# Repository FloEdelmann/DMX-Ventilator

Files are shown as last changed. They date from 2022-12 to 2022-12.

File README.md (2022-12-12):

# DMX-Ventilator

## Motivation

Wir waren im Dezember 2015 auf dem [Contact Indoor Festival München](https://www.facebook.com/events/544198745721461/ "Facebook-Versnataltung"). Was uns dort neben der Musik am meisten beeindruckt hat, waren die Ventilatoren, die als Effektgeräte hinter der Bühne im Zenith&nbsp;I heruntergelassen werden und sich drehen konnten. Die Flügel haben in einer einstellbaren Farbe geleuchtet und auch die Geschwindigkeit war in einem weiten Bereich regelbar.

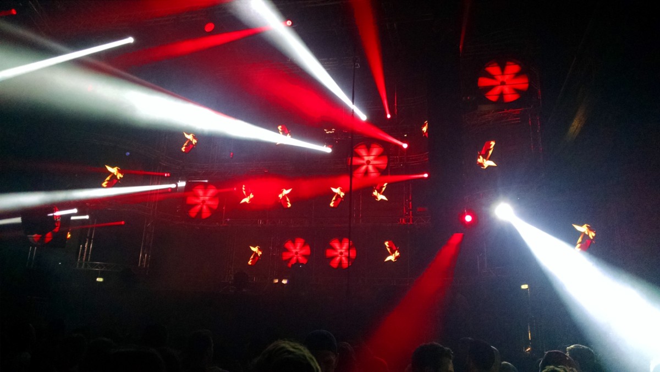
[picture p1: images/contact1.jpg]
Ventilatoren auf dem Contact-Festival 1

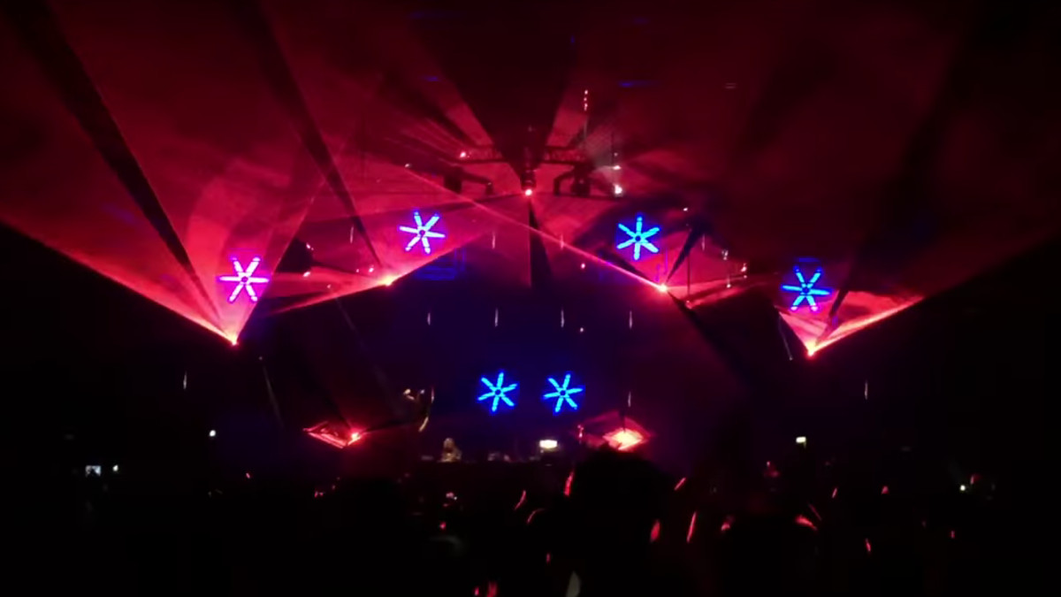
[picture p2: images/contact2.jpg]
Ventilatoren auf dem Contact-Festival 2


Auf YouTube gibt es sie auch in Bewegung zu sehen:
https://www.youtube.com/watch?v=OpufAzwtyVI (rot in verschiedenen Geschwindigkeiten)
https://www.youtube.com/watch?v=SzctCUNd09I (blau)

So etwas wollten wir jetzt auch auch!

## Planung

### Elektronik

Bei der Suche nach DMX-Selbstbau-Projekten verweist letztendlich fast jede Quelle auf [Hendrik Hölschers Seiten](http://www.hoelscher-hi.de/hendrik/wahl.htm). Sein [DMX-LED-Dimmer](http://www.hoelscher-hi.de/hendrik/light/dmxled.htm) hat schon einige Features, die auch unser Ventilator haben soll: Über DMX können 8 Kanäle gesteuert werden (zusätzlich sogar gestrobed), dank AVR-Microcontroller ist die Schaltung einfach zu programmieren und zu verändern und die Hardware ist sehr modular gehalten, sodass auch andere Projekte einfach realisiert werden können.

Es fehlt jedoch die Ansteuerung eines Motors. Außerdem wollen wir LED-Strips verwenden, da sie einfach zu montieren sind, und die brauchen noch eine extra Stromversorgung. Also muss eine zweite Platine her, die die Ansteuerungen übernimmt. Sie ist so gelayoutet, dass auch ein Lochraster-Aufbau möglich ist.

Beide Schaltungen hängen dann zusammen an einer 12V-<abbr title="Gleichspannung">DC</abbr>-Stromversorgung und werden über die 8-polige Steckerleiste miteinander verbunden.

Zum Programmieren des Microcontrollers werden über den ISP-Port die nötigen Anschlüsse herausgeführt. Da es jedoch ein standardisiertes 10-Pin-ISP-Interface gibt, das auch die gängigen [Programmieradapter](http://www.mikrocontroller.net/articles/AVR_In_System_Programmer) verwenden, habe ich mir ein zusätzliches Adapterkabel gebaut.

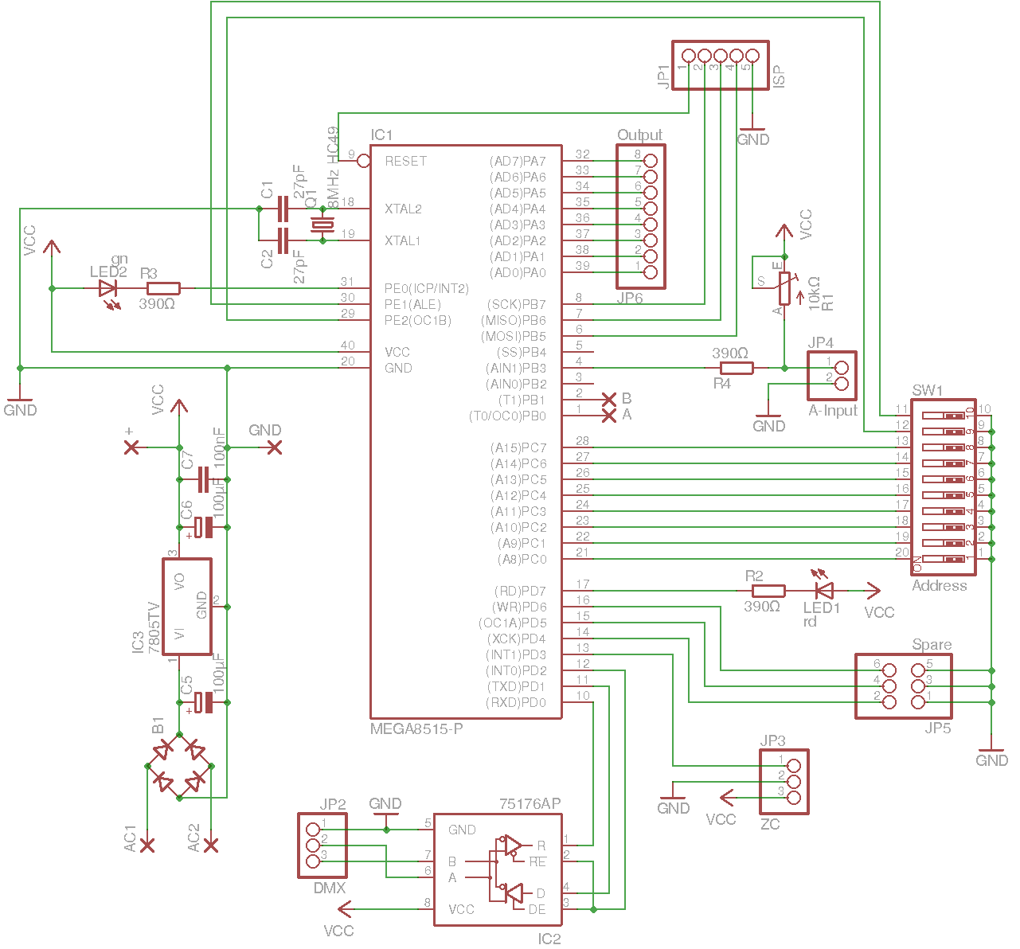
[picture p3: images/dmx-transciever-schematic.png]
Layout des DMX-Transcievers

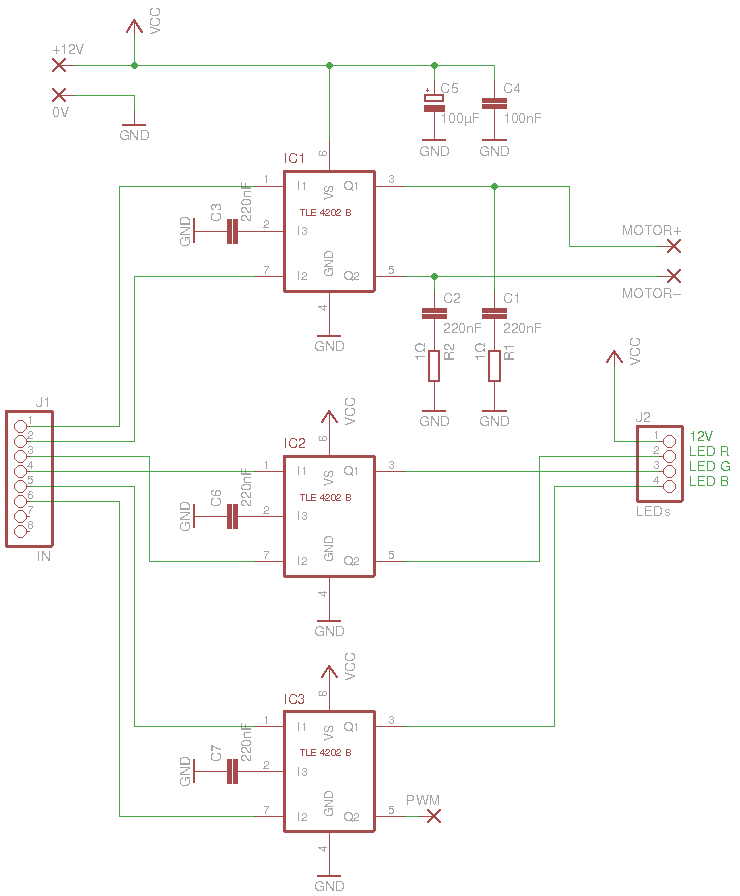
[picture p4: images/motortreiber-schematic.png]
Schaltplan des Motortreibers

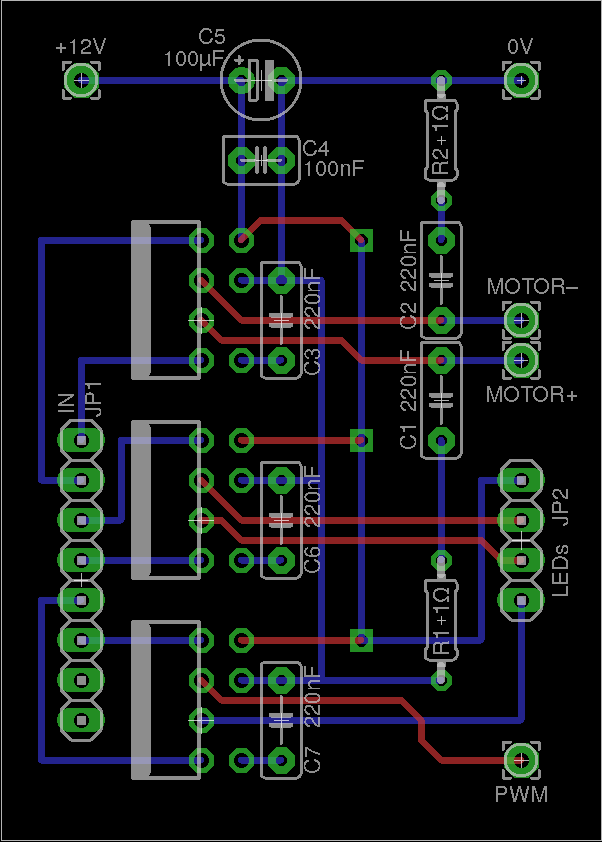
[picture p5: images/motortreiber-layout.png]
Layout des Motortreibers

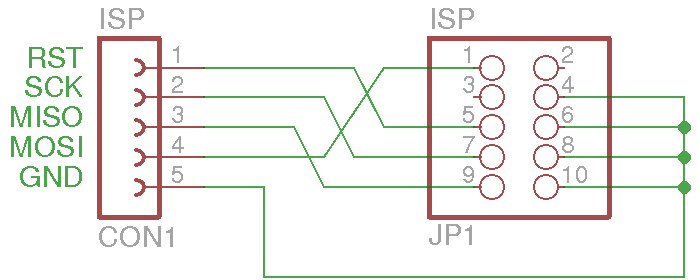
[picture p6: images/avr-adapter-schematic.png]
Anschlussplan des Adapterkabels

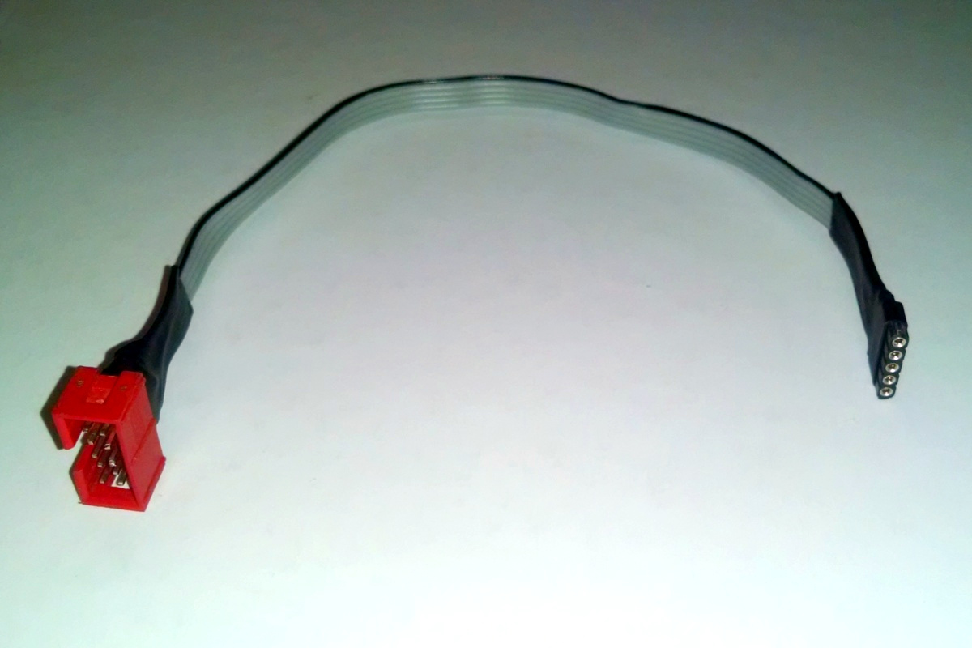
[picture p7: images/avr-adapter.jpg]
Adapterkabel

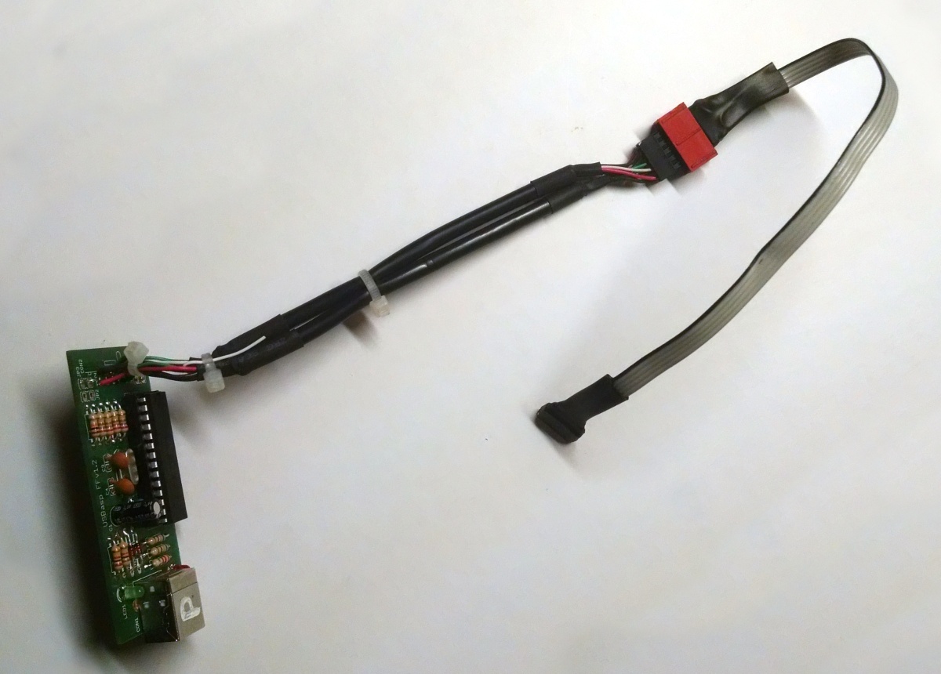
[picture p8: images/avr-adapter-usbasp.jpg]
Adapterkabel an der Programmierplatine USBasp


**Downloads für [EAGLE](http://www.cadsoft.de/download-eagle/):** [avr-adapter.sch](eagle/avr-adapter.sch), [dmx-transciever.sch](eagle/dmx-transciever.sch), [motortreiber.brd](eagle/motortreiber.brd), [motortreiber.sch](eagle/motortreiber.sch)

### Gehäuse & Mechanik

Am Motor wird eine Edelstahlwelle befestigt, die von einem Kugellager drehbar in Position gehalten wird. Die Rotorblätter sollen aus milchigem Plexiglas geschnitten werden, da diese als Lichtleiter bei der Anstrahlung mit den LED-Strips hoffentlich eine gute Ausleuchtung erzielen. Sie werden zwischen zwei großen Beilagscheiben mit mehreren Schrauben / Nieten befestigt und als ganzes von vorne an die Achse geschraubt.

Mit [Autodesk 123D Design](http://www.123dapp.com/design) lässt sich recht schnell ein vorzeigbares 3D-Modell erstellen. Dabei kann man schon vor dem physischen Aufbau Mängel in der Konstruktion erkennen und beheben.

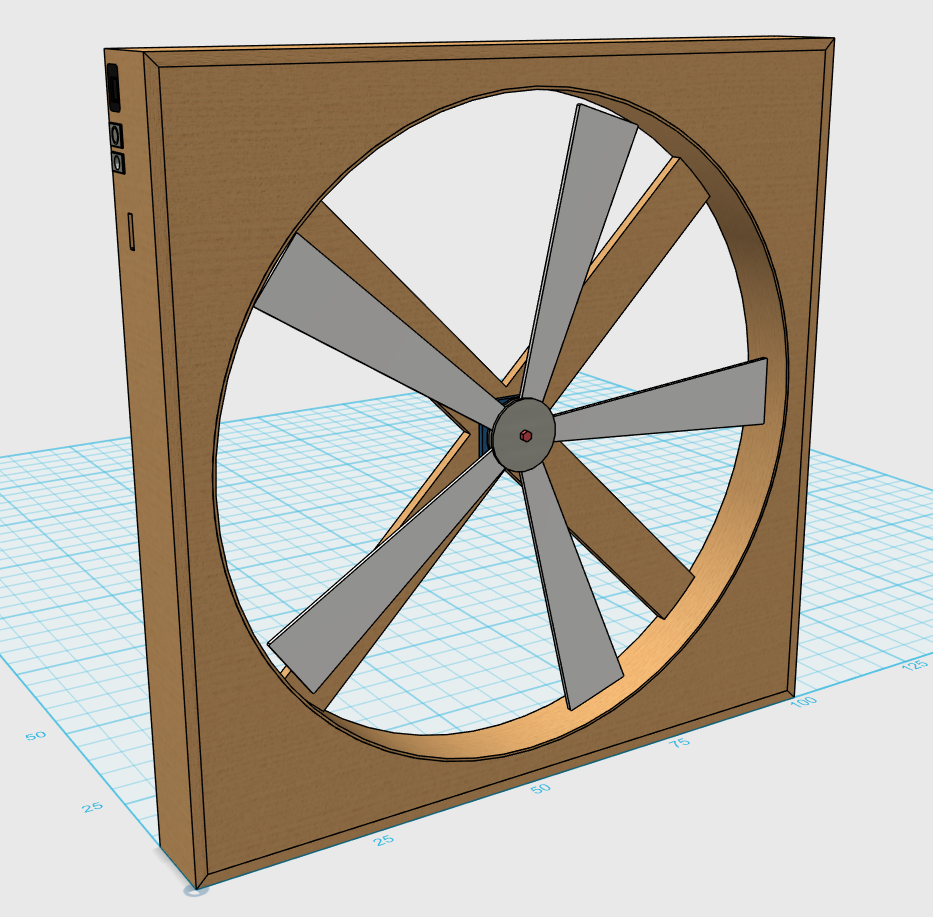
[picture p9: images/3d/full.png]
Gesamtansicht

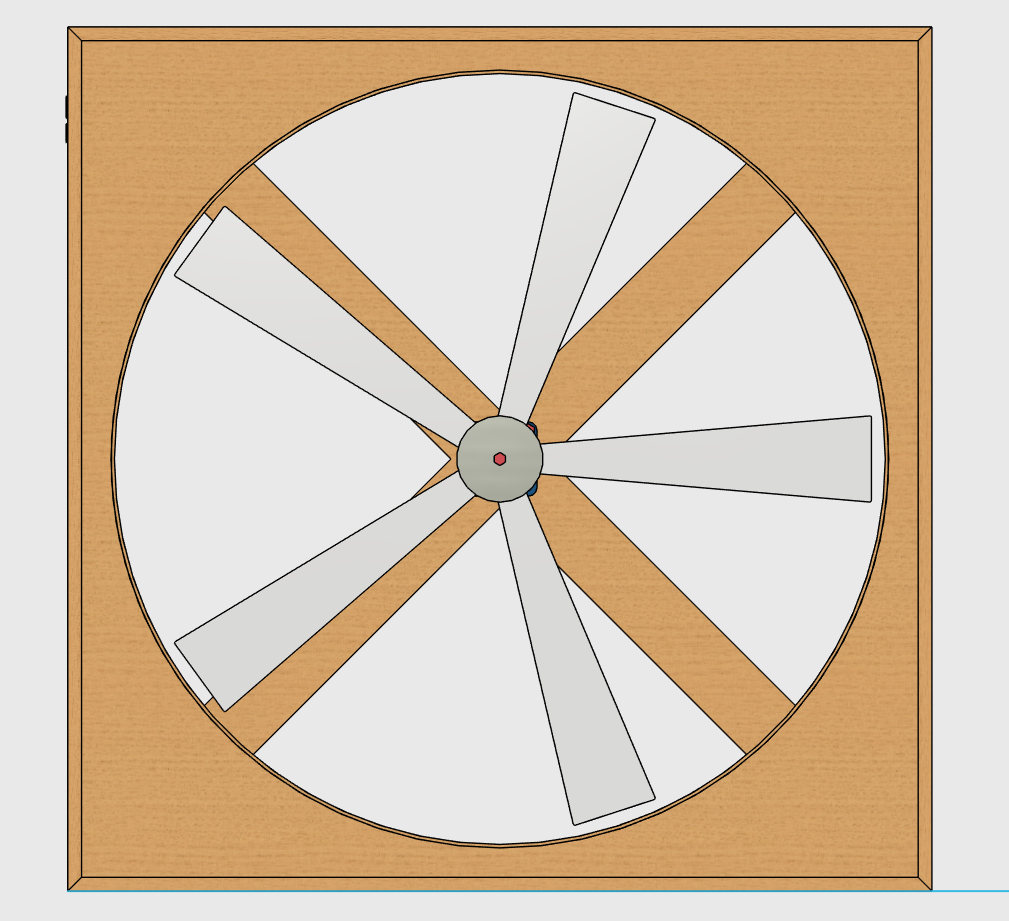
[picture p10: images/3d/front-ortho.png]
Frontansicht (orthografische Projektion)

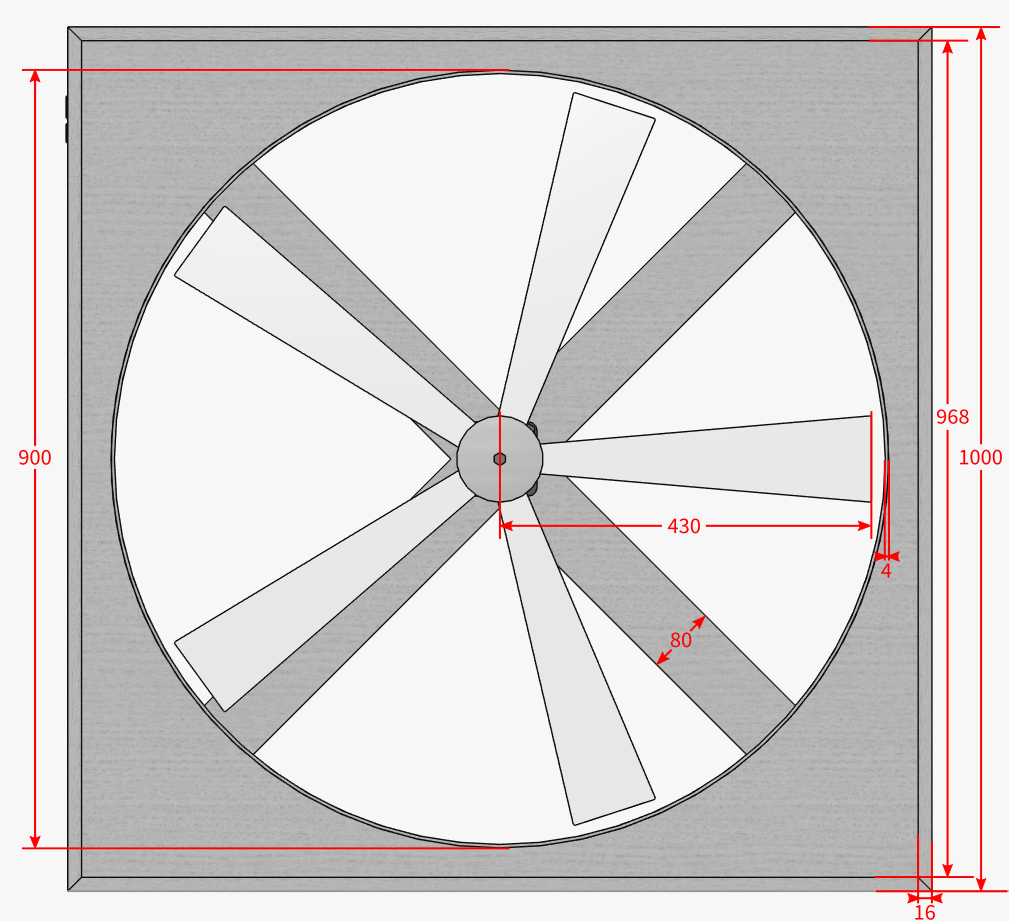
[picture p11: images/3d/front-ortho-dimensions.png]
Frontansicht mit Maßen

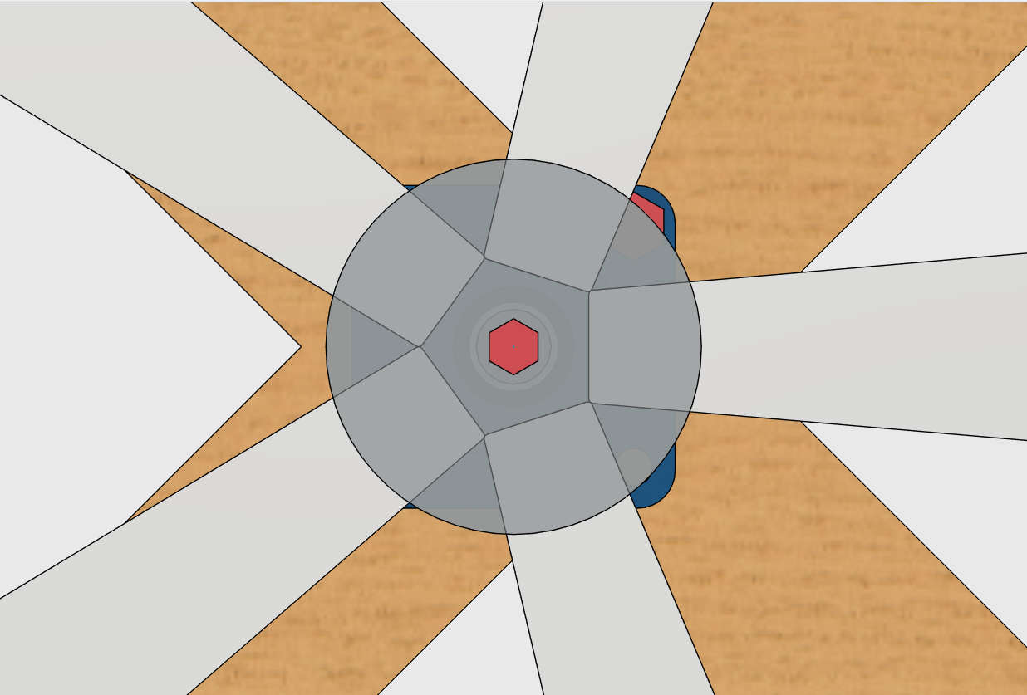
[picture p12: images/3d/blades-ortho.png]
Flügel (orthografisch)

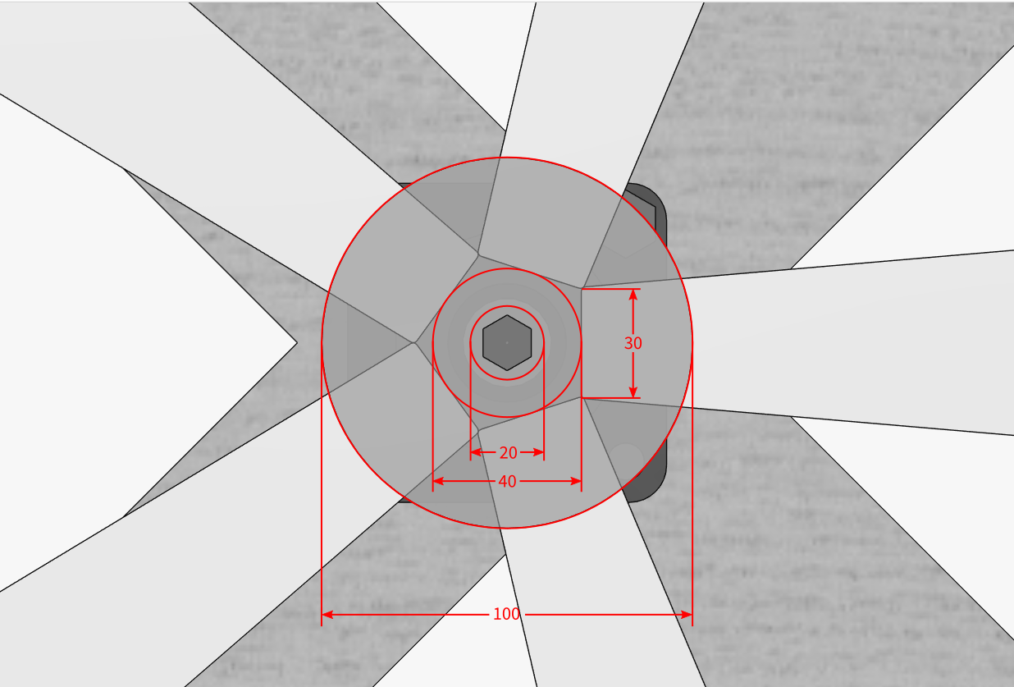
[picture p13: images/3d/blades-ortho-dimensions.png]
Flügel mit Maßen

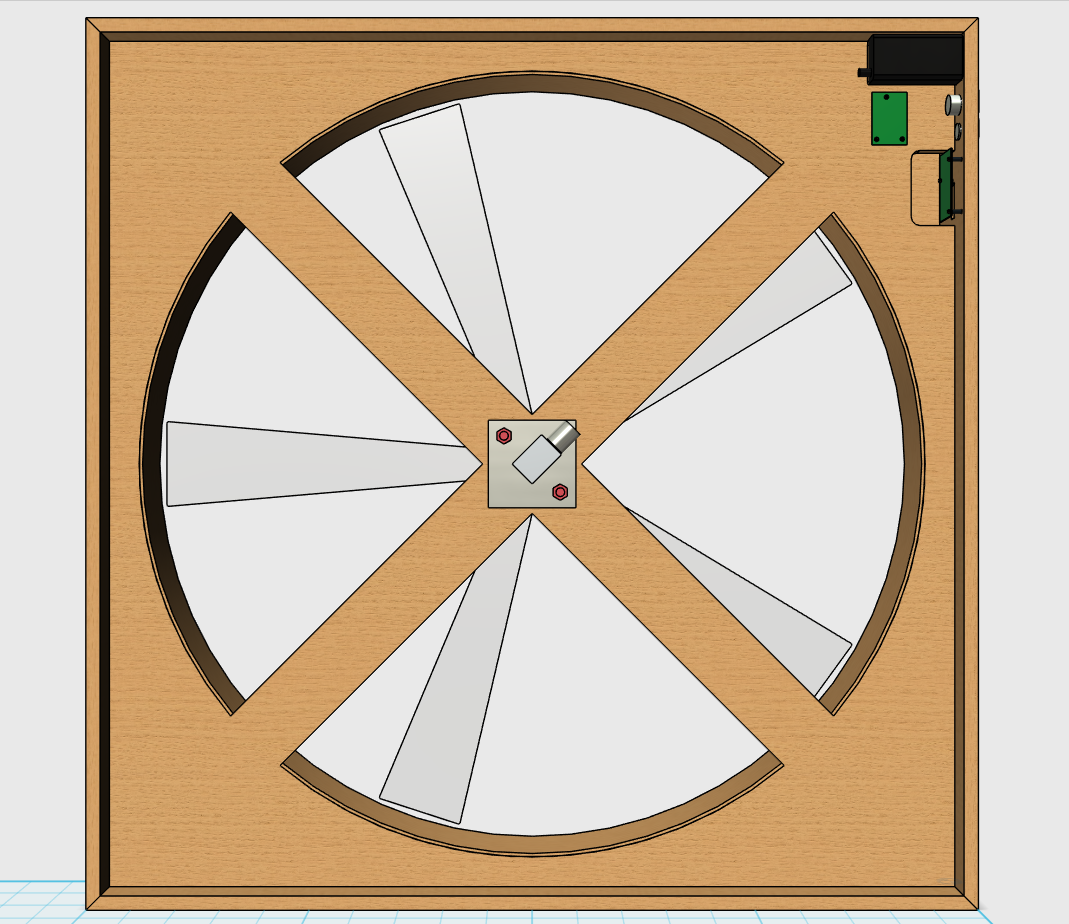
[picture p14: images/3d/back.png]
Rückansicht

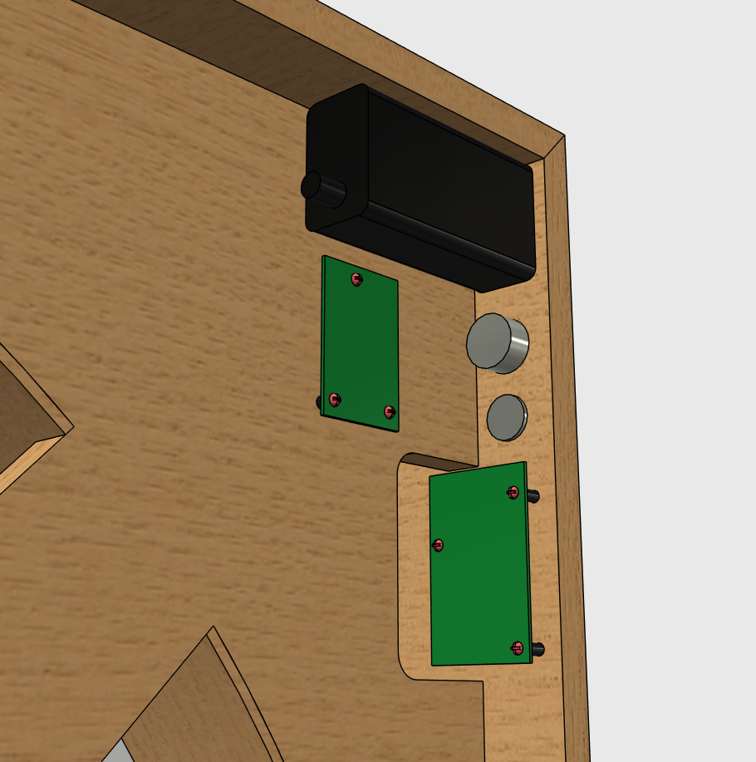
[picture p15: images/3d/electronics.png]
Elektronik

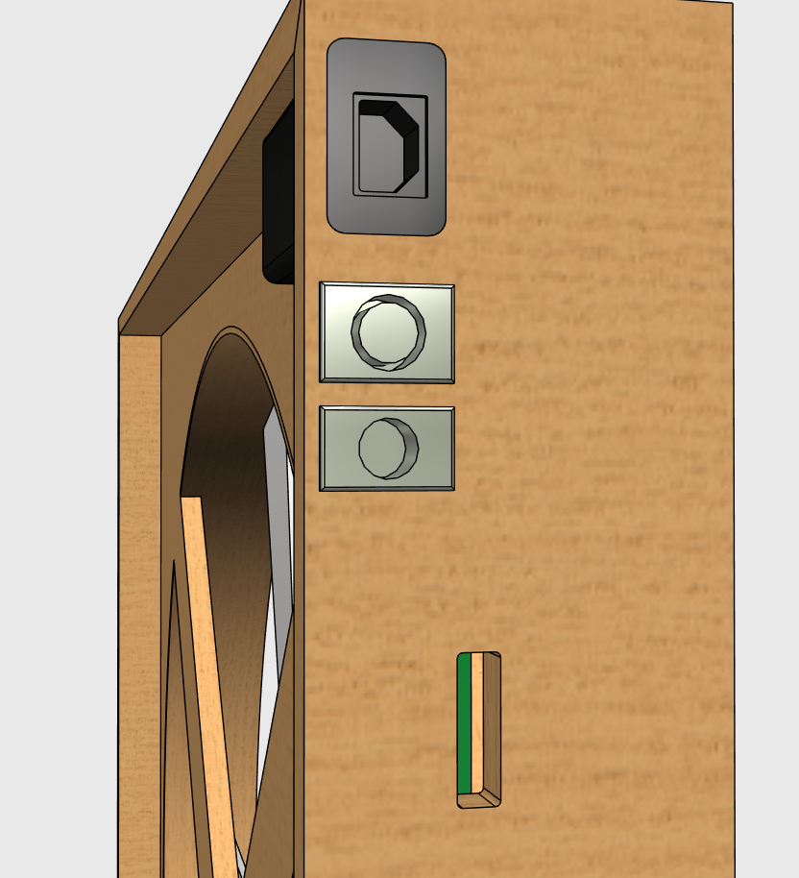
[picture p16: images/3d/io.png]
Anschlüsse mit Aussparung für DIP-Switch und Status-LEDs

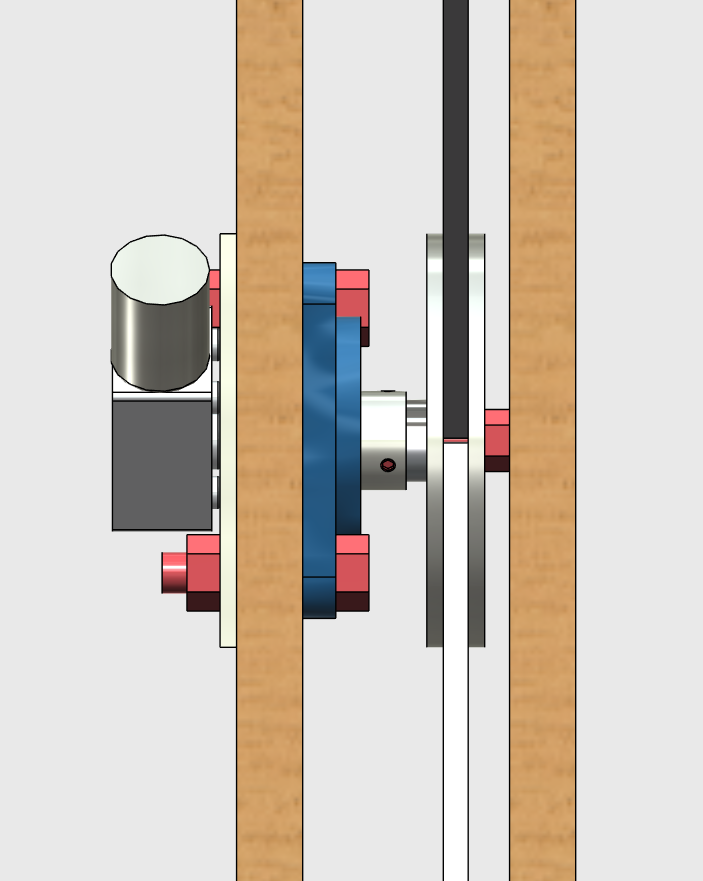
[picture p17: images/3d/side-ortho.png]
Seite (orthografisch)

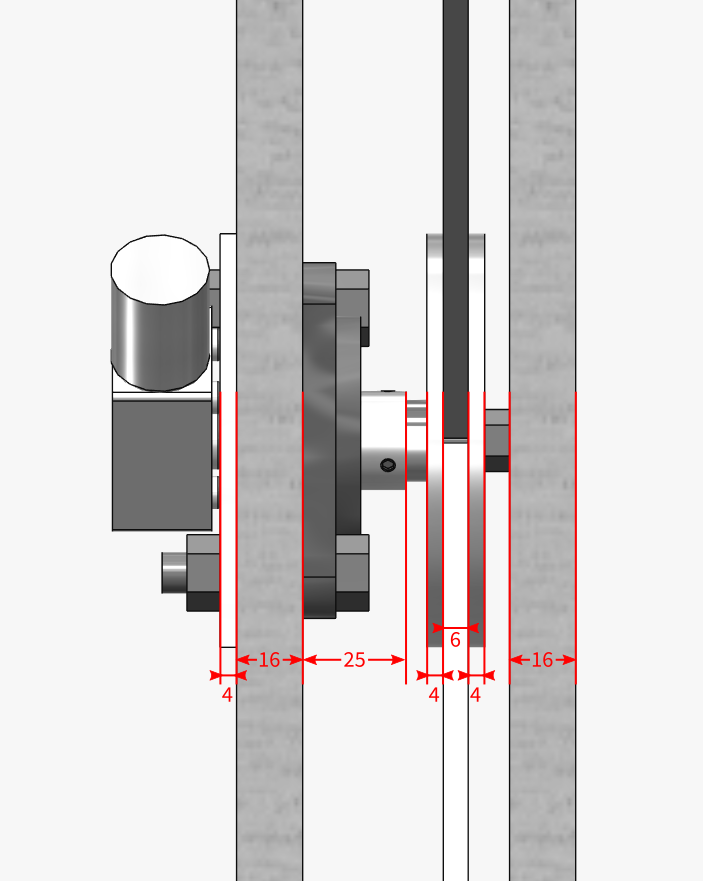
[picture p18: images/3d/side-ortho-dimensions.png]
Seite mit Maßen

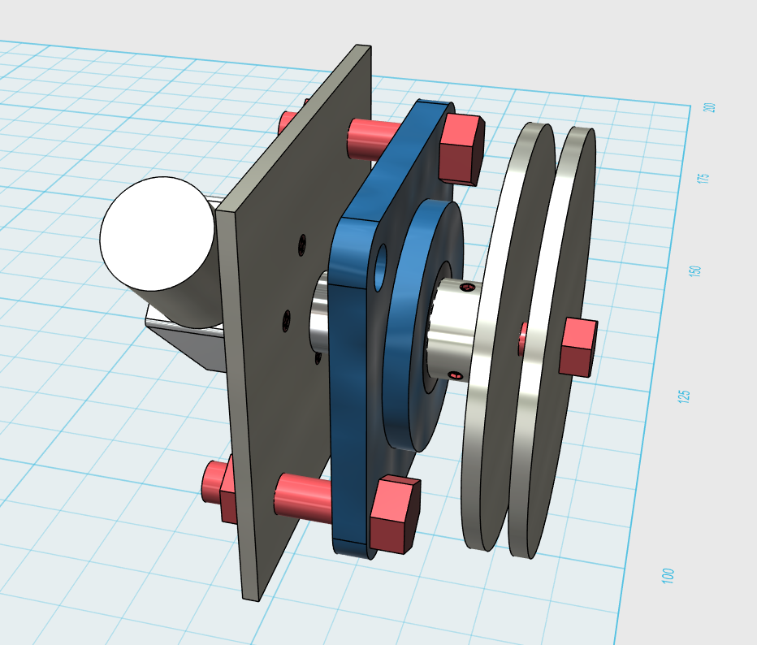
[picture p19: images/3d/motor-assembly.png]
Motor-Aufbau

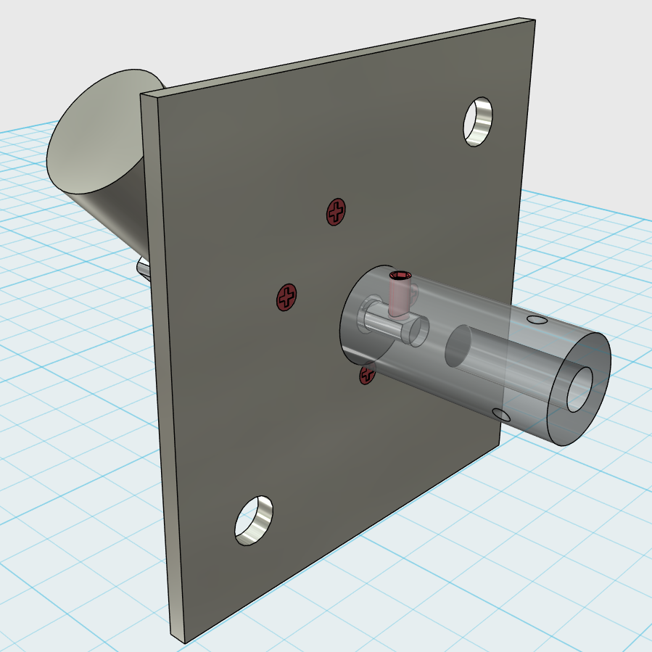
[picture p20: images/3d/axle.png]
Achse

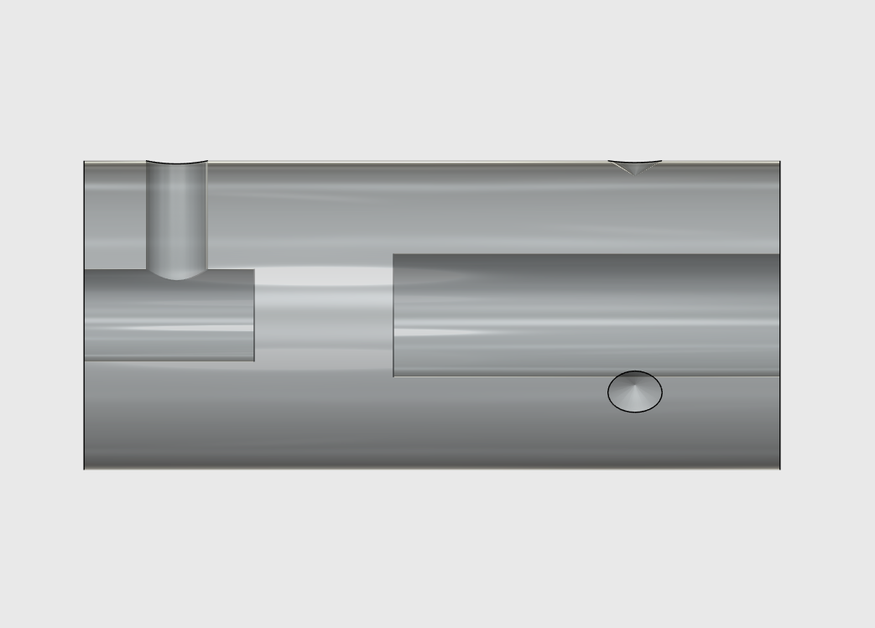
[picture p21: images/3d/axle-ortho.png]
Achse (orthografisch)

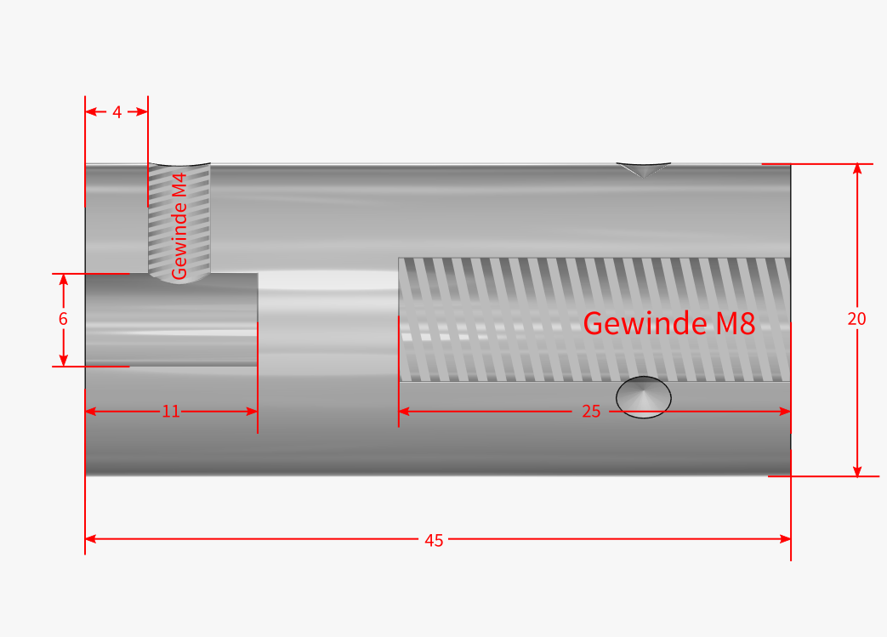
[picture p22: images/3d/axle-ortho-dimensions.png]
Achse mit Maßen


### Teile- und Bestellliste

| Stück | Bezeichnung | Link |
| -----:| --- | ---- |
| 1 | 12V-DC-Getriebemotor 200rpm | [eBay](http://www.ebay.de/itm/351368945189) |
| 1 | Neuer Motor | [Conrad](https://www.conrad.de/de/getriebemotor-12-v-modelcraft-rb350030-0a101r-130-227544.html) |
| 1 | RGB-LED-Strip 4m | [eBay](http://www.ebay.de/itm/151160889546) |
| 1 | 12V-DC-Netzteil 4A | [eBay](http://www.ebay.de/itm/151581215241) |
| 1 | Lochrasterplatine 4×6cm | [eBay](http://www.ebay.de/itm/261846070281) |
| 1 | Transciever-Board | [embedded projects](http://shop.embedded-projects.net/sonstige/dmx-transceiver.html) |
| 1 | 3-Pol-XLR-Einbaubuchse (DMX-In) | [Pollin](http://www.pollin.de/shop/dt/NTM2OTQ1OTk-/HiFi_Car_HiFi_Video_TV/Steckverbinder/Sonstiges/XLR_Einbaubuchse.html) |
| 1 | 3-Pol-XLR-Einbaustecker (DMX-Out)  | [Pollin](http://www.pollin.de/shop/dt/NDM2OTQ1OTk-/HiFi_Car_HiFi_Video_TV/Steckverbinder/Sonstiges/XLR_Einbaustecker.html) |
| | mehradriges Kabel (z.B. IDE-Kabel) | |
| 1 | Edelstahlwelle 50mm, ø 20mm | [eBay](http://www.ebay.de/itm/121103784726) |
| 1 | Flanschlager ø 20mm | [eBay](http://www.ebay.de/itm/251852780407) |
| | Acrylglas, 6mm | [eBay](http://www.ebay.de/itm/151269316675) |
| | Aluminium-Platte, 4mm | [eBay](http://www.ebay.de/itm/141345316955) |
| | Holz (Multiplex), 16mm | |
| | MDF, 4mm | |
| | Senkkopf-Holzschrauben | |
| 6 | Rundkopf-Holzschrauben | |
| 1 | Madenschraube M4 | |
| 1 | Metallschraube M8, 35mm | |
| 2 | Metallschraube M10, 30mm | |
| 2 | Mutter M10 | |
| 4 | Senkkopf-Metallschraube M2.5, 10mm | |
| 3 | Abstandshalter ca. 5mm | |
| 3 | Abstandshalter ca. 12mm | |

**Bestückung**

| Stück | Bezeichnung | Teilenamen Transciever / Motortreiber | Link |
| -----:| --- | --- | ---- |
| 1 | 10-Pol-DIP-Switch | SW1 / – | [eBay](http://www.ebay.de/itm/121855976441) |
| 1 | ATmega8515-P | IC1 / – | [eBay](http://www.ebay.de/itm/310716403642) |
| 1 | 75176AP | IC2 / – | [eBay](http://www.ebay.de/itm/381374573295) |
| 1 | 7805 | IC3 / – | [Pollin](http://www.pollin.de/shop/dt/ODU5OTI4OTk-/Bauelemente_Bauteile/Aktive_Bauelemente/Spannungsregler/Spannungsregler_ST_L7805CV.html) |
| 1 | IC-Sockel 40-polig | für IC1 / – | [Pollin](http://www.pollin.de/shop/dt/OTY5OTk1OTk-/Bauelemente_Bauteile/Mechanische_Bauelemente/IC_Fassungen_Adapterplatinen/IC_Fassung_40_polig.html) |
| 1 | IC-Sockel 8-polig | für IC2 / – | [Pollin](http://www.pollin.de/shop/dt/Nzc5OTk1OTk-/Bauelemente_Bauteile/Mechanische_Bauelemente/IC_Fassungen_Adapterplatinen/IC_Praezisionsfassung_8_polig.html) |
| 3 | TLE-4202-B | – / IC1, IC2, IC3 | [Pollin](http://www.pollin.de/shop/dt/NTU5ODk4OTk-/Bauelemente_Bauteile/Aktive_Bauelemente/IC/TLE4202B_STS_B57928.html) |
| 1 | Quartz 8MHz | Q1 / – | [Pollin](http://www.pollin.de/shop/dt/MTk5OTY3OTk-/Bauelemente_Bauteile/Passive_Bauelemente/Quarze_Oszillatoren/Quarz.html) |
| 2 | Kondensator 27pF<br />(**genau!**) | C1, C2 / – | [Conrad](https://www.conrad.de/de/keramik-scheibenkondensator-27-pf-100-vdc-5-x-h-35-mm-x-4-mm-1-st-457175.html) |
| 2 | Kondensator 100nF | C7 / C4 | [Pollin](http://www.pollin.de/shop/dt/OTA4OTk3OTk-/Bauelemente_Bauteile/Passive_Bauelemente/Kondensatoren/Folien_Kondensator_100_nF.html) |
| 5 | Kondensator 220nF | – / C1, C2, C3, C6, C7 | [Pollin](http://www.pollin.de/shop/dt/OTgzOTk3OTk-/Bauelemente_Bauteile/Passive_Bauelemente/Kondensatoren/MKT_Kondensator.html) |
| 3 | Elko 100µF | C5, C6 / C5 | [Pollin](http://www.pollin.de/shop/dt/MTM2OTg3OTk-/Bauelemente_Bauteile/Passive_Bauelemente/Elkos_Goldcaps/Elko_100_F_25_V_10_Stueck_NIPPON_CHEMI_CON_KZE.html) |
| 1 | LED rot 3mm | LED1 / – | [Pollin](http://www.pollin.de/shop/dt/MjY5OTc4OTk-/Bauelemente_Bauteile/Aktive_Bauelemente/LEDs/LED.html) |
| 1 | LED grün 3mm | LED2 / – | [Pollin](http://www.pollin.de/shop/dt/OTA5ODc4OTk-/Bauelemente_Bauteile/Aktive_Bauelemente/LEDs/LED_KINGBRIGHT_L_934SGDLK_gruen_3_mm_10_Stueck.html) |
| 1 | Poti 10kΩ | R1 / – | [Pollin](http://www.pollin.de/shop/dt/MTM3OTU3OTk-/Bauelemente_Bauteile/Passive_Bauelemente/Potis_Trimmer_Encoder/Potentiometer_PIHER_PT_10.html) |
| 2 | Widerstand 1Ω<br />(4,7Ω geht auch) | – / R1, R2 | [Pollin](http://www.pollin.de/shop/dt/MTQyOTc3OTk-/Bauelemente_Bauteile/Passive_Bauelemente/Widerstaende/Metallfilm_Widerstaende.html) |
| 3 | Widerstand 390Ω<br />(470Ω geht auch) | R2, R3, R4 / – | [Pollin](http://www.pollin.de/shop/dt/ODIyOTc3OTk-/Bauelemente_Bauteile/Passive_Bauelemente/Widerstaende/Metallfilm_Widerstaende.html) |
| 1 | Stiftleiste 1×2 | JP4 / – | [Pollin](http://www.pollin.de/shop/dt/OTQ0ODQ1OTk-/Bauelemente_Bauteile/Mechanische_Bauelemente/Steckverbinder_Klemmen/Stiftleiste_vergoldet_1x_20_polig_10_Stueck.html) (rowspan=5) |
| 2 | Stiftleiste 1×3 | JP2, JP3 / – | |
| 1 | Stiftleiste 1×4 | – / JP2 | |
| 1 | Stiftleiste 1×5 | JP1 / – | |
| 2 | Stiftleiste 1×8 | JP6 / JP1 | |
| 1 | Stiftleiste 2×3 | JP5 / – | [Pollin](http://www.pollin.de/shop/dt/NDkyOTQ1OTk-/Bauelemente_Bauteile/Mechanische_Bauelemente/Steckverbinder_Klemmen/Stiftleiste.html) |
| 1 | Stiftbuchse 1×3 | | [Conrad](https://www.conrad.de/de/buchsenleiste-praezision-anzahl-reihen-1-polzahl-je-reihe-36-w-p-products-153-036-1-50-10-1-st-736427.html) (rowspan=4) |
| 1 | Stiftbuchse 1×4 | | |
| 1 | Stiftbuchse 1×2 | | |
| 2 | Stiftbuchse 1×8 | | |

## Aufbau der Elektronik

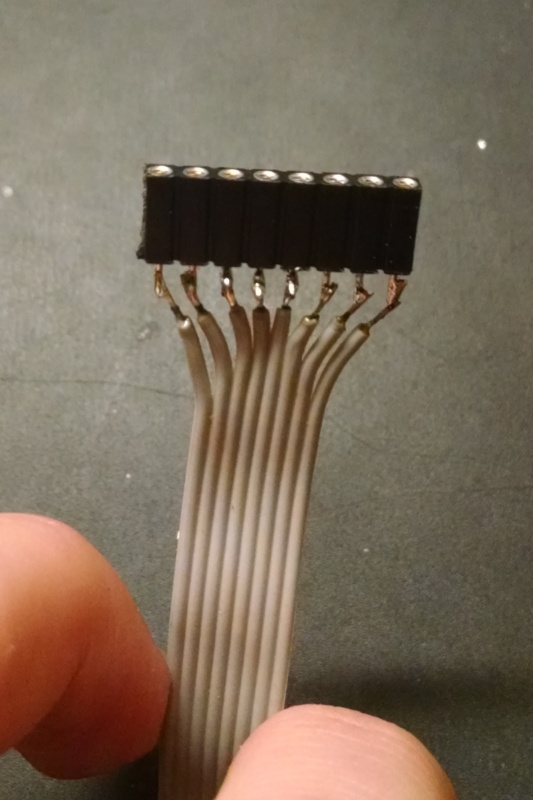
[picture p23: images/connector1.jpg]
8-poliges Verbindungskabel: IDE-Kabel mit Stiftbuchse

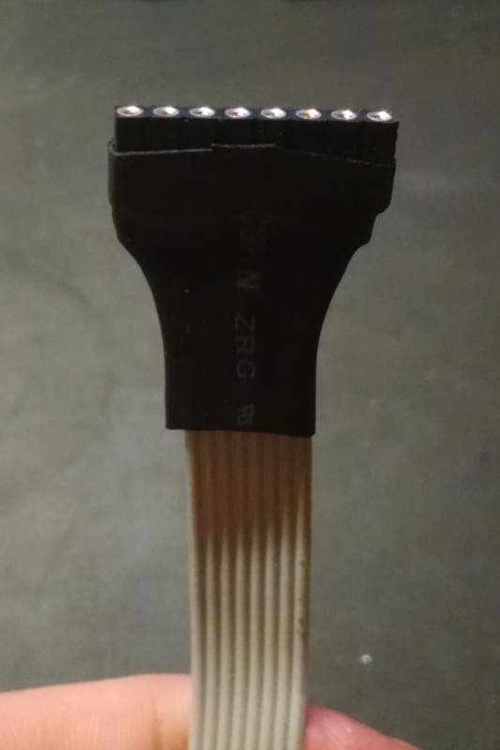
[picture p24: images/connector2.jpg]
Verbindungskabel mit Schrumpfschlauch

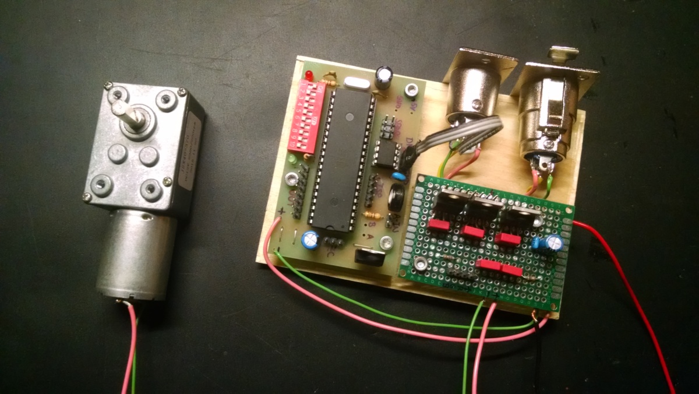
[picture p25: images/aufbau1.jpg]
temporärer Aufbau auf Holzbrett

## TODO: Verbindungskabel falsch rum
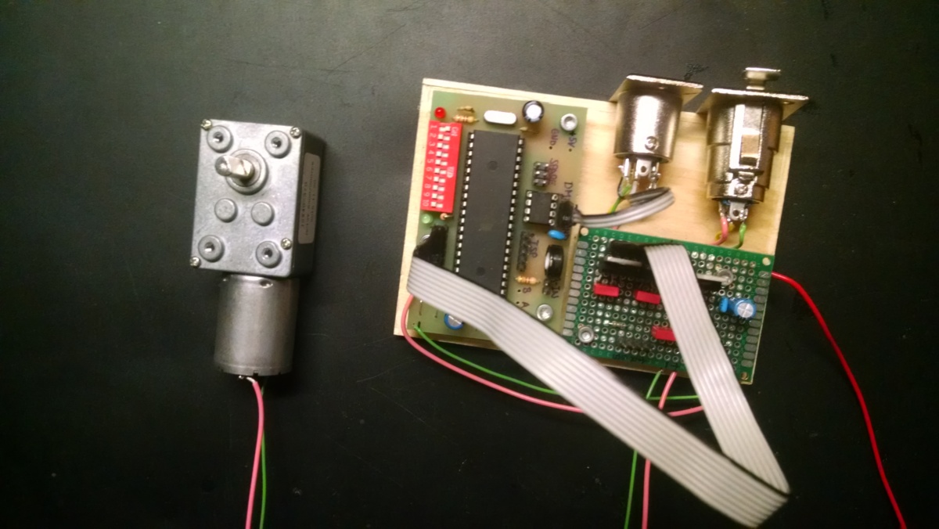
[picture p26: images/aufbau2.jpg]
Aufbau mit angeschlossenem Verbindungskabel

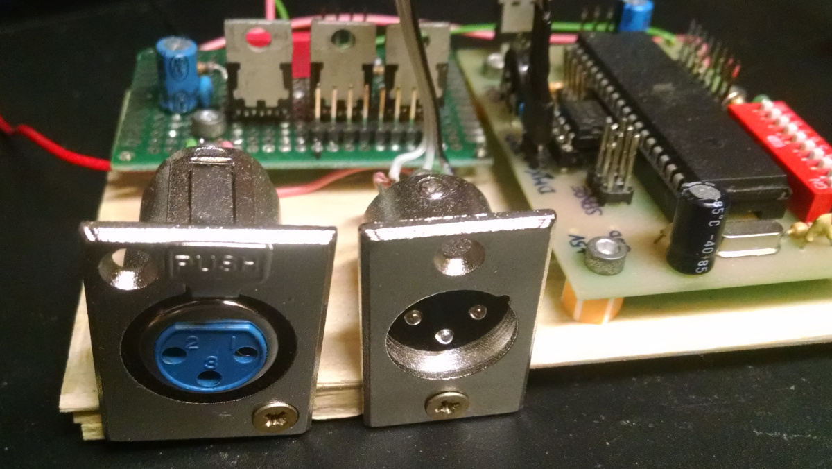
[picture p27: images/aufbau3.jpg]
DMX-Out und -In

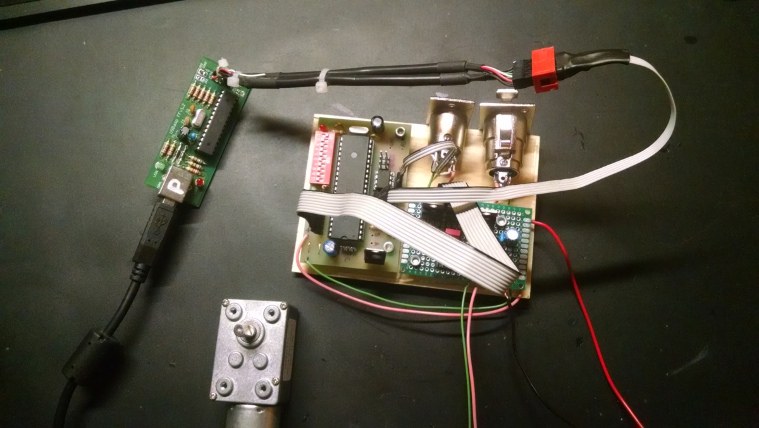
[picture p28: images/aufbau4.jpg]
angeschlossener Programmieradapter


## Programmieren

Der folgende Abschnitt bezieht sich auf das Programmieren unter Ubuntu Linux. Bei anderen Betriebssystemen müssen entsprechend andere Programme zum Assemblieren und Übertragen des Codes verwendet werden.

Als Programmier-Interface verwende ich [USBasp](http://www.fischl.de/usbasp/), das es als fertige Platine oder als Bausatz zum Selberlöten gibt. Nach Anschluss des Programmieradapters (siehe Foto oben) kann mit dem folgenden Befehl das Testfile von Hendrik Hölschers Webseite ([board.hex](http://www.hoelscher-hi.de/hendrik/light/ressources/board.hex)) übertragen werden:

    sudo avrdude -p atmega8515 -c usbasp -B 3 -U flash:w:board.hex

* `sudo`: ohne Root-Rechte bekomme ich eine Fehlermeldung (*access denied*)
* `-p atmega8515`: Angabe des verwendeten Microcontrollers
* `-c usbasp`: Angabe des Programmier-Interfaces
* `-B 3`: kleinster Wert für die `bit clock period`, damit USBasp erkannt wird
* `-U flash:w:board.hex`: schreibe das Testfile in den Flash-Speicher

**Testfunktionen:**

| DIP-Switch | Bedeutung |
| --- | --- |
| Alle DIPs off | Blinken der roten LED zeigt an, dass das Testfile in den Flash geladen wurde. |
| Alle DIPs an  | Leuchten der grünen LED zeigt an, dass alle DIP-Schalter korrekt verlötet sind. |
| DIP1 an | Leuchten der grünen LED zeigt an, dass die fuse bits angepasst wurden. |
| DIP2 an | Leuchtet die grüne LED, liegt ein korrektes DMX-Signal an. Ein Blinken indiziert, dass D+ und D- verpolt sind. |
| DIP3 an | Leuchtet die grüne LED, funktioniert die angeschlossene ZC-Detection. (für uns irrelevant) |

Mit dem Testprogramm habe ich festgestellt, dass alles passt, aber die Fuse bits noch nicht gesetzt wurden. Zuerst wollen wir die aktuell gesetzten Bits lesen: `sudo avrdude -p atmega8515 -c usbasp -B 3 -n` liefert `Fuses OK (E:FF, H:D9, L:E1)`. Durch Herumspielen mit dem [AVR Fuse Calculator](http://www.engbedded.com/fusecalc), bis die Werte mit denen in http://www.hoelscher-hi.de/hendrik/light/ressources/an011.pdf übereinstimmen, bin ich auf den folgenden Befehl gekommen:

    sudo avrdude -p atmega8515 -c usbasp -B 3 -U lfuse:w:0x3f:m -U hfuse:w:0x9d:m

Danach lief das Testprogramm problemlos durch.

### `udev`-Regel

Um `avrdude` nicht jedes Mal mit Root-Rechten ausführen zu müssen, fügt man eine neue *udev rule* hinzu. Dazu erstellt man die Datei `/etc/udev/rules.d/60-usbasp.rules` mit dem folgenden Inhalt:

    # USBasp
    SUBSYSTEM=="usb", ATTRS{idVendor}=="16c0", ATTRS{idProduct}=="05dc", GROUP="adm", MODE="0666"

Danach wird die neue Datei mit `sudo service udev restart` eingelesen und man kann künftig `avrdude` ohne Root-Rechte zum Übertragen verwenden.

### Assembler und Makefile

Danach geht es an den eigentlichen Projekt-Code (`LED.asm` inkl. `lib_asm.asm`).

Als Assembler (der `.asm`-Dateien in übertragbare `.hex`-Dateien assembliert) verwenden wir `avra`.

Damit wir zum Assemblieren und Übertragen nicht immer zwei einzelne Befehle ausführen müssen, erstellen wir uns ein **Makefile**:

    file = LED.hex

    all: $(file)
        avrdude -p atmega8515 -c usbasp -B 3 -U flash:w:$(file)

    %.hex: %.asm
        avra -I "/usr/share/avra" $*.asm

    fuse:
        avrdude -p atmega8515 -c usbasp -B 3 -U lfuse:w:0x3f:m -U hfuse:w:0x9d:m

    test:
        avrdude -p atmega8515 -c usbasp -B 3 -U flash:w:board.hex

**Achtung:** Die Einrückung muss hier mit Tabs geschehen!

In `/usr/share/avra` liegen die Microcontroller-Definitionsdateien, also insbesondere auch `m8515def.inc`, das wir für unser Projekt brauchen. Mit der Option `-I` weisen wir `avra` an, auch in diesem Verzeichnis nach den Include-Dateien zu suchen.

Beim ersten Ausführen mit `make` gab es Fehlermeldungen, dass `avra` diese Kommentare nicht kennt: `/* … */` und `// …`. Daher habe ich sie durch `; …` ersetzt. Danach konnte ich bereits ohne Probleme assemblieren und übertragen und das Programm funktioniert tadellos.

Danach habe ich die beiden Dateien zusammengeführt, um leichter zu verstehen, was wo passiert.

Jetzt kann es an die eigenen Erweiterungen gehen!

### DIP-Switch

Die DIP-Schalter-Stellungen sollen unverändert weiterhin gelten:
**DIP1 - DIP9** stellen die DMX-Adresse dar (Bit 0 - 8 in aufsteigender Reihenfolge)
**DIP10** aktiviert den Standalone Mode, womit folgendes gilt:

| DIP-Switch | Funktion |
| ---:| --- |
| 1 - 3 | Programm |
| 5 - 8 | Geschwindigkeit |
| 9 | Strobe |

Die auswählbaren Programme müssen aber entsprechend angepasst bzw. durch neue ersetzt werden, damit diese die verschiedenen LED-Farben und den Motor entsprechend ansteuern. Zum Testen reichen aber erst mal die vorgegebenen.

### Standalone-Programme

Ich habe den IC2 (75176B), welcher für die Übersetzung von DMX in das vom Microcontroller verständliche USART zuständig ist, in China bestellt. Da dieser wegen der langen Lieferzeit noch nicht da ist, mache ich mich zuerst an die Standalone-Programme. Diese werden durch den [DIP-Switch](#dip-switch) bestimmt und können daher ohne anliegendes DMX-Signal getestet werden.

Ein vorgegebenes Programm (DIP2 an) sieht z.B. so aus:

    .org PAT1                   ; Lauflicht
    .dw 0b0000000001
    .dw 0b0000000010
    .dw 0b0000000100
    .dw 0b0000001000
    .dw 0b0000010000
    .dw 0b0000100000
    .dw 0b0001000000
    .dw 0b0010000000
    .dw 0b1100000000

Dabei stehen die einzelnen Zeilen für die unterschiedlichen Zustände, die ineinander übergefaded werden sollen. Das erste Bit ist nur beim letzten Zustand gesetzt, um das Ende des Programms zu kennzeichnen. Danach folgen die Werte für die Ausgänge `A` (ungenutzt), `M+`, `M-`, `R`, `G`, `B`, `P` (ungenutzt, aber aufs zweite Board herausgeführt) sowie zwei weitere nicht benutzte Ausgänge.

Der Motor dreht sich im Uhrzeigersinn, wenn `M+` und `M-` auf `0` und `1` gesetzt werden bzw. gegen den Uhrzeigersinn für `1` und `0`. Liegt an beiden Ausgängen der selbe Pegel an, dreht der Motor sich nicht.

Die LEDs sind an, wenn der entsprechende Ausgang auf *low* gesetzt wird.

Das folgende Beispiel zeigt also einen RGB-Fader, bei dem der Motor immer im Uhrzeigersinn dreht:

<pre>
.dw 0b0<span style="color:#aaa">0</span><span style="color:#d80">01</span><span style="color:red">0</span>11<span style="color:#aaa">000</span>
.dw 0b0<span style="color:#aaa">0</span><span style="color:#d80">01</span><span style="color:red">0</span><span style="color:#0c0">0</span>1<span style="color:#aaa">000</span>
.dw 0b0<span style="color:#aaa">0</span><span style="color:#d80">01</span>1<span style="color:#0c0">0</span>1<span style="color:#aaa">000</span>
.dw 0b0<span style="color:#aaa">0</span><span style="color:#d80">01</span>1<span style="color:#0c0">0</span><span style="color:#00f">0</span><span style="color:#aaa">000</span>
.dw 0b0<span style="color:#aaa">0</span><span style="color:#d80">01</span>11<span style="color:#00f">0</span><span style="color:#aaa">000</span>
.dw 0b<strong>1</strong><span style="color:#aaa">0</span><span style="color:#d80">01</span><span style="color:red">0</span>1<span style="color:#00f">0</span><span style="color:#aaa">000</span>
</pre>

Die anderen Programme könnt ihr im Code selbst anschauen.

### DMX-Channels

Die DMX-Channels sollen wie folgt aussehen:

| DMX-Channel | Funktion |
| ---:| --- |
| 0 | <p>Motor</p><table><tbody><tr><td align="right">0 - 3</td><td>aus</td></tr><tr><td align="right">4 - 119</td><td>gegen den Uhrzeigersinn (immer langsamer)</td></tr><tr><td align="right">120 - 139</td><td>aus (Mitte)</td></tr><tr><td align="right">140 - 255</td><td>im Uhrzeigersinn (immer schneller)</td></tr></tbody></table> |
| 1 | rote LEDs |
| 2 | grüne LEDs |
| 3 | blaue LEDs |
| 4 | LED-Strobe (optional) |
| 5 | Master-Helligkeit für LEDs (optional) |

Mehr Channels brauchen wir nicht.

Um die Farb-Channels schon einmal richtig zu mappen, habe ich im Label `pwm_exit` den Abschnitt angepasst, der die Werte vom `DMX_FIELD` auf das `PWM_FIELD` kopiert, von wo aus sie im nächsten Timer-Durchlauf ausgegeben werden.

Der Motor erfordert etwas mehr Aufwand, da von einem Channel aus zwei Ausgänge gesteuert werden sollen. Ich habe mir die Funktion `eval_strobe_freq` zum Vorbild genommen und auch von der main loop aus die neue Funktion `eval_motor_speed` aufgerufen. Diese springt je nach DMX-Wert in verschiedene Sublabels. Von dort aus wird der DMX-Wert auf einen Bereich von 0 bis 115 gebracht und mit diesem Wert aus `MOTOR_MAP` der jeweils auszugebene PWM-Wert (0 bis 255) geholt und ins `PWM_FIELD` geschrieben. Das ist nötig, da wir leider nicht einfach mit einer Fließkommazahl multiplizieren können (etwa `y = x * 255/115;`).

Die Strobe-Funktion war ja schon eingebaut und musste nur so angepasst werden, dass sie auf DMX-Kanal 4 statt 1 hört (einfach) und nur die LEDs und nicht den Motor flasht. Dazu habe ich im Label `pwm` den Code so geändert, dass alle Kanäle immer normal auf den jeweiligen Wert, und danach beim Blackout mit Hilfe eines logischen Oders nur die LED-Kanäle auf 1 gesetzt werden.

#### Motor-Bremse

Da der Motor nicht allzu schnell von einem Wert auf einen anderen beschleunigen bzw. abbremsen sollte, habe ich die Funktion `eval_motor_speed` danach so abgeändert, dass in jedem Durchlauf der Soll-Wert (`DMX_FIELD` und `MOTOR_MAP`) und der Ist-Wert (`PWM_FIELD`) verglichen werden und der Output nur um eins inkrementiert oder dekrementiert wird.

Da das aber viel zu schnell abläuft, vergleiche ich vorher zusätzlich, dass die beiden Register `checkMotorL` und `checkMotorH` gleich null sind. Dieses Quasi-16-bit-Register wird vom Interrupt-Handler `pwm`, der bei jedem Overflow von `Timer0` aufgerufen wird, je um eins inkrementiert. Das war dann aber wiederum viel zu langsam, sodass `checkMotorH` sofort wieder auf null zurückgesetzt wird, sobald es den Wert 20 erreicht hat. Die Geschwindigkeit sieht im Testbetrieb vernünftig aus, eventuell muss an dem Wert aber noch gefeilt werden, sobald der Motor eingebaut ist.

Leider hat es unseren ersten Motor mit dem Wert von 20 zerschossen. Wir haben danach einen leistungsfähigeren besorgt, trotzdem wollten wir auf Nummer sicher gehen und haben den Wert auf 40 verdoppelt. Da dann aber das Anfahren sehr, sehr langsam ist, erlauben wir ein Inkrementieren öfter als ein Dekrementieren.

### Hilfe bei Assembler-Kommandos

Da man häufig mal nachschauen muss, was die einzelnen Assembler-Kommandos bedeuten, habe ich hier eine kleine Hilfe programmiert: Einfach Befehl oder Direktive eingeben (z.B. `jmp` oder `.equ`) und es werden Einzelheiten angezeigt.

<input type="text" id="asm-help-input" placeholder="Assembler-Hilfe" />

<script type="text/javascript" src="asm-help.js"></script>

## Mechanischer Aufbau

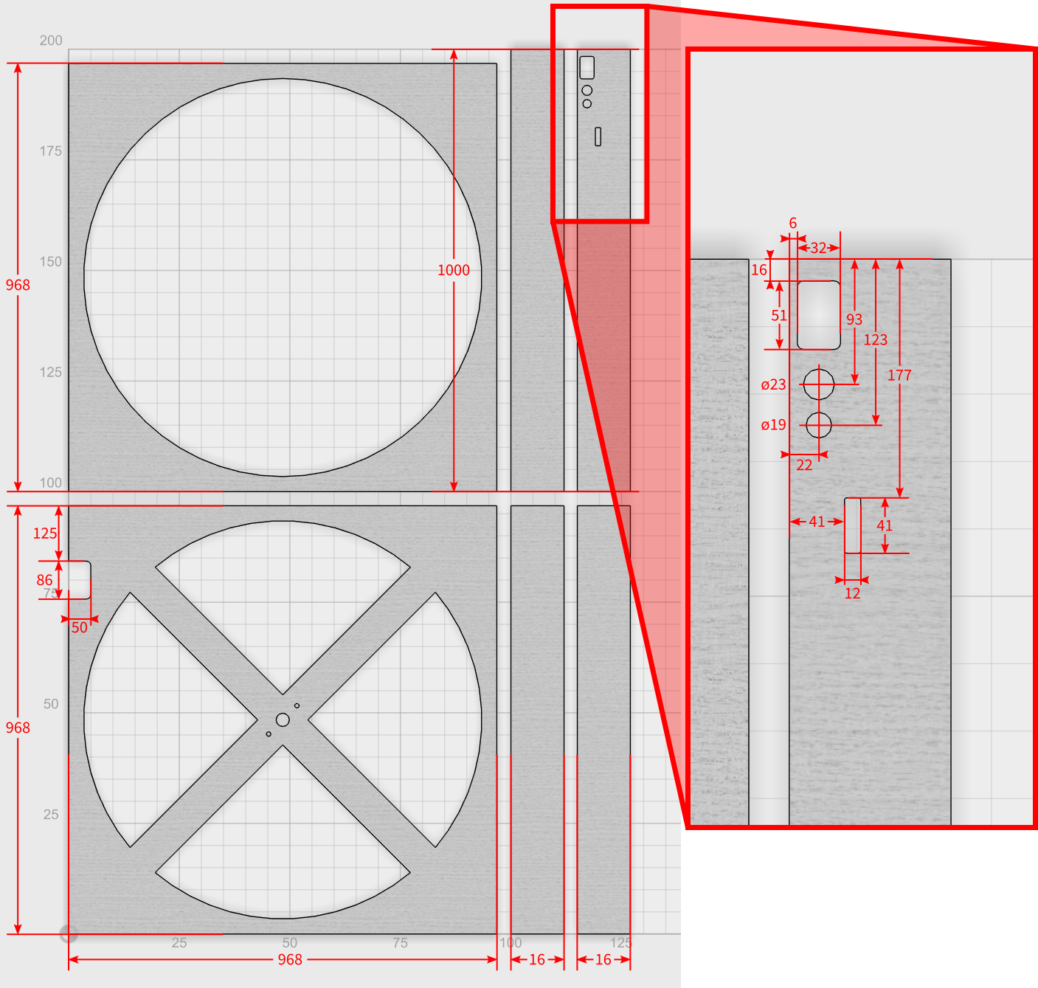
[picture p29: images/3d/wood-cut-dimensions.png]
Holzschnitt


*(readme is not complete; see rest of the repository for more information)*

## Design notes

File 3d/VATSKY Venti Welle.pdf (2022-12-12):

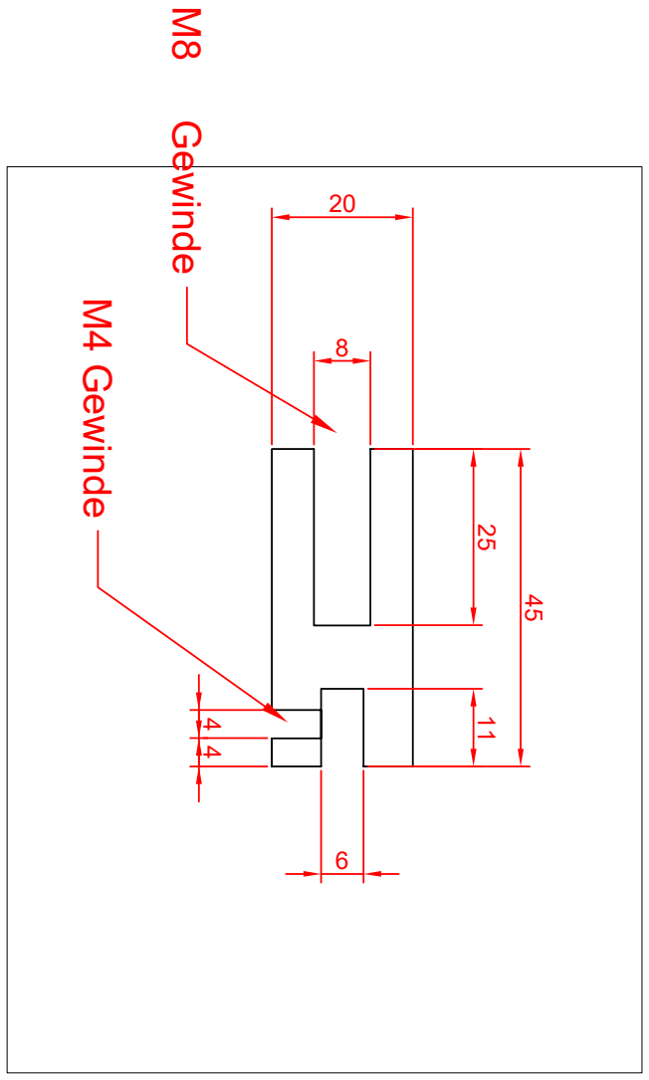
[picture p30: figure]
208 11 25 6 ⁴ ⁴ M8 Gewinde M4 Gewinde

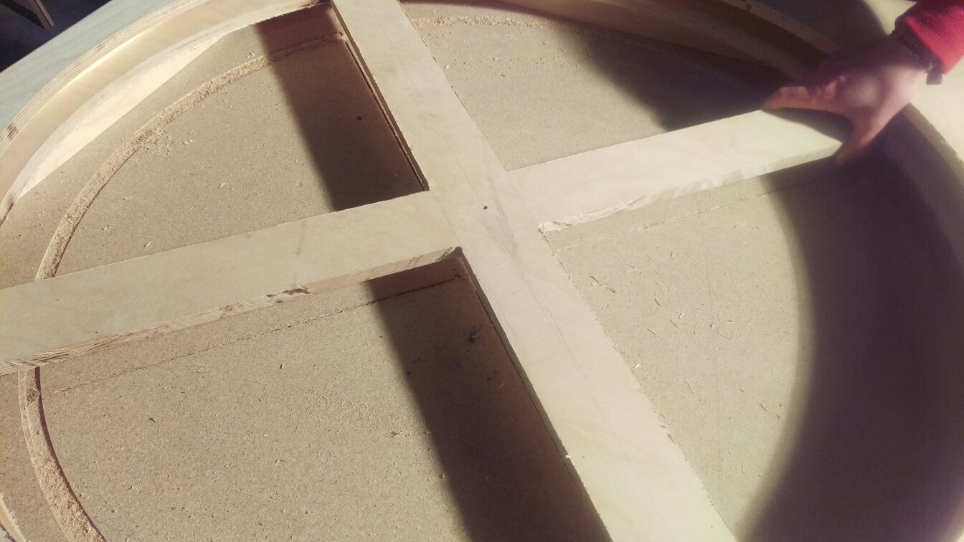
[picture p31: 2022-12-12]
images/orig/gehaeuse/IMG-20160402-WA0004.jpg

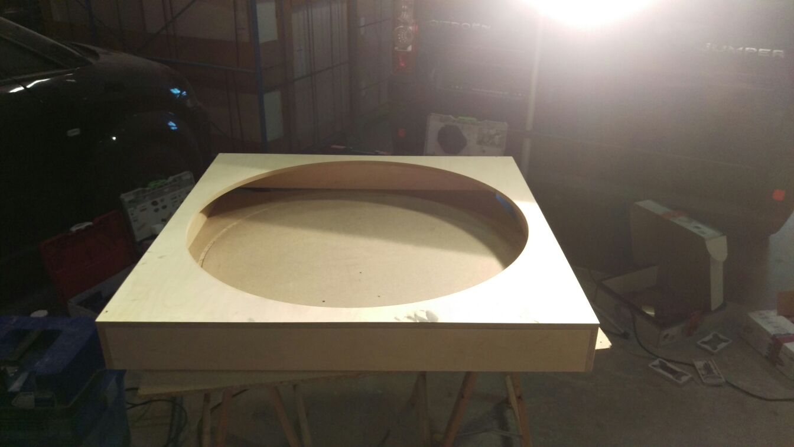
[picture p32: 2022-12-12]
images/orig/IMG-20160402-WA0012.jpg

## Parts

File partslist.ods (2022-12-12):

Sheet: Bestellliste
Bestellliste
Teil | Transciever | Motortreiber | sonstige | insg. | Teile Transciever | Teile Motortreiber | Link
7805 | 1 | 0 | 7 | 10 | IC3 |  | http://www.pollin.de/shop/dt/ODU5OTI4OTk-/Bauelemente_Bauteile/Aktive_Bauelemente/Spannungsregler/Spannungsregler_ST_L7805CV.html
10x-DIP-Switch | 1 | 0 | 0 | 3 | SW1 |  | http://www.ebay.de/itm/121855976441?_trksid=p2057872.m2749.l2649&ssPageName=STRK%3AMEBIDX%3AIT
75176AP | 1 | 0 | 7 | 10 | IC2 |  | http://www.ebay.de/itm/381374573295?_trksid=p2057872.m2749.l2649&ssPageName=STRK%3AMEBIDX%3AIT
capacitor 100nF | 1 | 1 | 0 | 6 | C7 | C4 | daheim
capacitor 220nF | 0 | 5 | 0 | 15 |  | C1, C2, C3, C6, C7 | http://www.pollin.de/shop/dt/OTgzOTk3OTk-/Bauelemente_Bauteile/Passive_Bauelemente/Kondensatoren/MKT_Kondensator.html
capacitor 27pF | 2 | 0 | 0 | 6 | C1, C2 |  | https://www.conrad.de/de/keramik-scheibenkondensator-27-pf-100-vdc-5-x-h-35-mm-x-4-mm-1-st-457175.html
elko 100µF | 2 | 1 | 0 | 9 | C5, C6 | C5 | daheim
LED green | 1 | 0 | 0 | 3 | LED2 |  | daheim
LED red | 1 | 0 | 0 | 3 | LED1 |  | daheim
MEGA8515-P | 1 | 0 | 0 | 3 | IC1 |  | http://www.ebay.de/itm/310716403642?_trksid=p2057872.m2749.l2649&ssPageName=STRK%3AMEBIDX%3AIT
poti 10kΩ | 1 | 0 | 1 | 4 | R1 |  | http://www.pollin.de/shop/dt/MTM3OTU3OTk-/Bauelemente_Bauteile/Passive_Bauelemente/Potis_Trimmer_Encoder/Potentiometer_PIHER_PT_10.html
Quartz 8MHz | 1 | 0 | 0 | 3 | Q1 |  | http://www.pollin.de/shop/dt/MTk5OTY3OTk-/Bauelemente_Bauteile/Passive_Bauelemente/Quarze_Oszillatoren/Quarz.html
resistor 1Ω | 0 | 2 | 0 | 6 |  | R1, R2 | daheim
resistor 390Ω | 3 | 0 | 0 | 9 | R2, R3, R4 |  | daheim
Stiftleiste 1x2 | 1 | 0 | 0 | 3 | A-Input |  | http://www.pollin.de/shop/dt/OTQ0ODQ1OTk-/Bauelemente_Bauteile/Mechanische_Bauelemente/Steckverbinder_Klemmen/Stiftleiste_vergoldet_1x_20_polig_10_Stueck.html
Stiftleiste 1x3 | 2 | 0 | 0 | 6 | DMX, ZC
Stiftleiste 1x4 | 0 | 1 | 0 | 3 |  | LEDs
Stiftleiste 1x5 | 1 | 0 | 0 | 3 | ISP
Stiftleiste 1x8 | 1 | 1 | 0 | 6 | Output | Input
Stiftleiste 2x3 | 1 | 0 | 0 | 3 | Spare |  | http://www.pollin.de/shop/dt/NDkyOTQ1OTk-/Bauelemente_Bauteile/Mechanische_Bauelemente/Steckverbinder_Klemmen/Stiftleiste.html
Stiftbuchse 1x3 | 1 | 0 | 0 | 3 |  |  | https://www.conrad.de/de/buchsenleiste-praezision-anzahl-reihen-1-polzahl-je-reihe-36-w-p-products-153-036-1-50-10-1-st-736427.html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
Stiftbuchse 1x4 | 0 | 1 | 0 | 3
Stiftbuchse 1x2 | 0 | 1 | 0 | 3
Stiftbuchse 1x8 | 1 | 1 | 0 | 6
TLE-4202-B | 0 | 3 | 0 | 9 |  | IC1, IC2, IC3 | http://www.pollin.de/shop/dt/NTU5ODk4OTk-/Bauelemente_Bauteile/Aktive_Bauelemente/IC/TLE4202B_STS_B57928.html
Motor | 0 | 3 | 0 | 9 |  |  | http://www.ebay.de/itm/Untersetzung-8300RPM-200-rpm-2-Pin-Anschluss-Schnecken-getriebemotor-DC12V-/351368945189
Transciever-Board | 1 | 0 | 0 | 3 |  |  | http://shop.embedded-projects.net/sonstige/dmx-transceiver.html
Lochrasterplatine | 0 | 1 | 0 | 3 |  |  | http://www.ebay.de/itm/261846070281?_trksid=p2057872.m2749.l2649&ssPageName=STRK%3AMEBIDX%3AIT
DMX-In | 1 | 0 | 1 | 4 |  |  | http://www.pollin.de/shop/dt/NTM2OTQ1OTk-/HiFi_Car_HiFi_Video_TV/Steckverbinder/Sonstiges/XLR_Einbaubuchse.html
DMX-Out | 1 | 0 | 1 | 4 |  |  | http://www.pollin.de/shop/dt/NDM2OTQ1OTk-/HiFi_Car_HiFi_Video_TV/Steckverbinder/Sonstiges/XLR_Einbaustecker.html
Sockel 40pol | 1 | 0 | 1 | 4 |  |  | http://www.pollin.de/shop/dt/OTY5OTk1OTk-/Bauelemente_Bauteile/Mechanische_Bauelemente/IC_Fassungen_Adapterplatinen/IC_Fassung_40_polig.html
Sockel 8pol | 1 | 0 | 2 | 5 |  |  | http://www.pollin.de/shop/dt/Nzc5OTk1OTk-/Bauelemente_Bauteile/Mechanische_Bauelemente/IC_Fassungen_Adapterplatinen/IC_Praezisionsfassung_8_polig.html
Netzteil | 1 | 0 | 0 | 3 |  |  | http://www.ebay.de/itm/151581215241

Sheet: Kostenübersicht
Kostenübersicht
Rechnung | Datum | Betrag | Versand | exkl. | Gesamt | Link
eBay: 3x Motor | 08.12.15 | 40,50 € | 0,00 € |  | 40,50 € | http://www.ebay.de/itm/Untersetzung-8300RPM-200-rpm-2-Pin-Anschluss-Schnecken-getriebemotor-DC12V-/351368945189
eBay: 3x ATmega8515-16PU | 20.01.16 | 11,56 € | 2,30 € |  | 13,86 € | http://payments.ebay.de/ws/eBayISAPI.dll?ViewPaymentStatus&transId=647996630021&itemid=310716403642
eBay: 20 tlg. Lochrasterplatine | 22.01.16 | 14,75 € | 0,00 € |  | 14,75 € | http://payments.ebay.de/ws/eBayISAPI.dll?ViewPaymentStatus&transId=1757349855016&itemid=261846070281
eBay: 3x 10-DIP-Schalter | 21.01.16 | 3,90 € | 4,00 € |  | 7,90 € | http://payments.ebay.de/ws/eBayISAPI.dll?ViewPaymentStatus&transId=1583864704002&itemid=121855976441
eBay: 10x SN75176B | 21.01.16 | 1,52 € | 0,00 € |  | 1,52 € | http://payments.ebay.de/ws/eBayISAPI.dll?ViewPaymentStatus&transId=677689782025&itemid=381374573295
Pollin: Bauteile | 21.01.16 | 24,93 € | 4,95 € | 3,75 € | 26,13 € | https://www.pollin.de/shop/bestellstatus.html
Conrad: 27pF-Kondensatoren | 24.01.16 | 1,10 € | 0,00 € |  | 1,10 € | https://www.conrad.de/de/account/orders.html
eBay: 2x LED-Strip | 27.01.16 | 21,60 € | 0,00 € |  | 21,60 € | http://vod.ebay.de/vod/FetchOrderDetails?itemid=151160889546&transid=1360066385005&viewpaymentstatus=
Conrad: Stiftbuchsen | 29.01.16 | 8,07 € | 0,00 € |  | 8,07 € | https://www.conrad.de/de/buchsenleiste-praezision-anzahl-reihen-1-polzahl-je-reihe-36-w-p-products-153-036-1-50-10-1-st-736427.html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
embedded-projects: Transciever-Platine | 21.01.16 | 17,85 € | 3,95 € |  | 21,80 € | https://shop.embedded-projects.net/account/orders
eBay: 2 Flanschlager | 04.03.16 | 13,90 € | 0,00 € |  | 13,90 € | http://www.ebay.de/itm/251852780407
eBay: Rundstahl-Welle | 04.03.16 | 4,70 € | 4,90 € |  | 9,60 € | http://www.ebay.de/itm/121103784726
eBay: 3x Netzteil | 07.03.16 | 19,47 € | 2,00 € |  | 21,47 € | http://www.ebay.de/itm/151581215241
eBay: Abstandshalter | 06.04.16 | 3,95 € | 0,00 € |  | 3,95 € | http://www.ebay.de/itm/231900935523
Conrad: 2x Motor | 25.04.16 | 44,43 € | 0,00 € |  | 44,43 € | https://www.conrad.de/de/getriebemotor-12-v-modelcraft-rb350030-0a101r-130-227544.html
Fliegengitter
Folie
Alu
Plexiglas
 |  |  |  | Gesamt: | 250,58 €

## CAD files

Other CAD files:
src/LED.obj

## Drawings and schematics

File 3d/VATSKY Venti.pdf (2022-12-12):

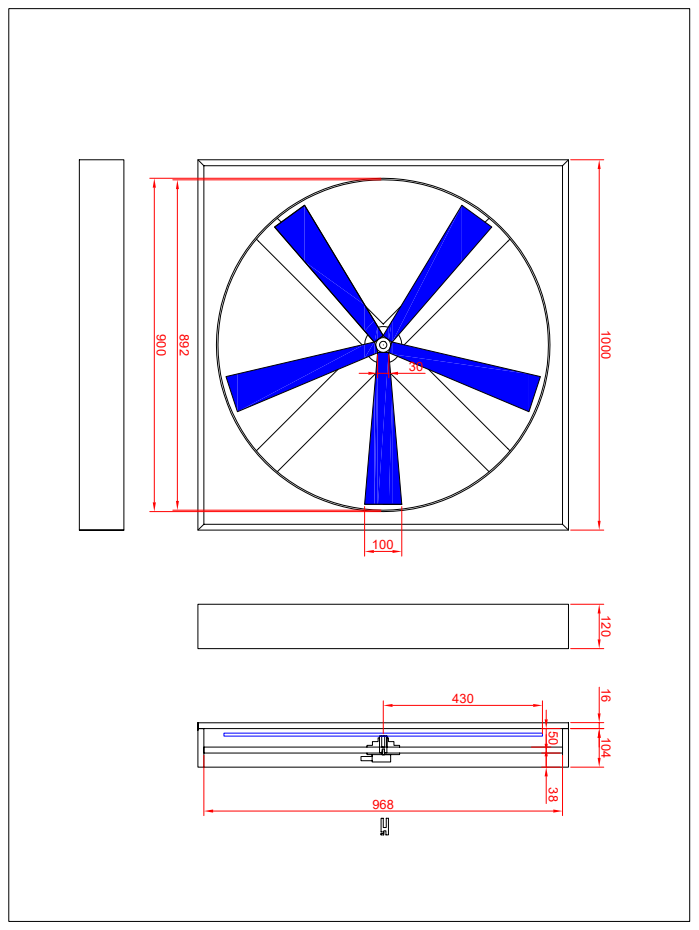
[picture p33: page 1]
430 ⁹⁰⁰ ⁸⁹² 30

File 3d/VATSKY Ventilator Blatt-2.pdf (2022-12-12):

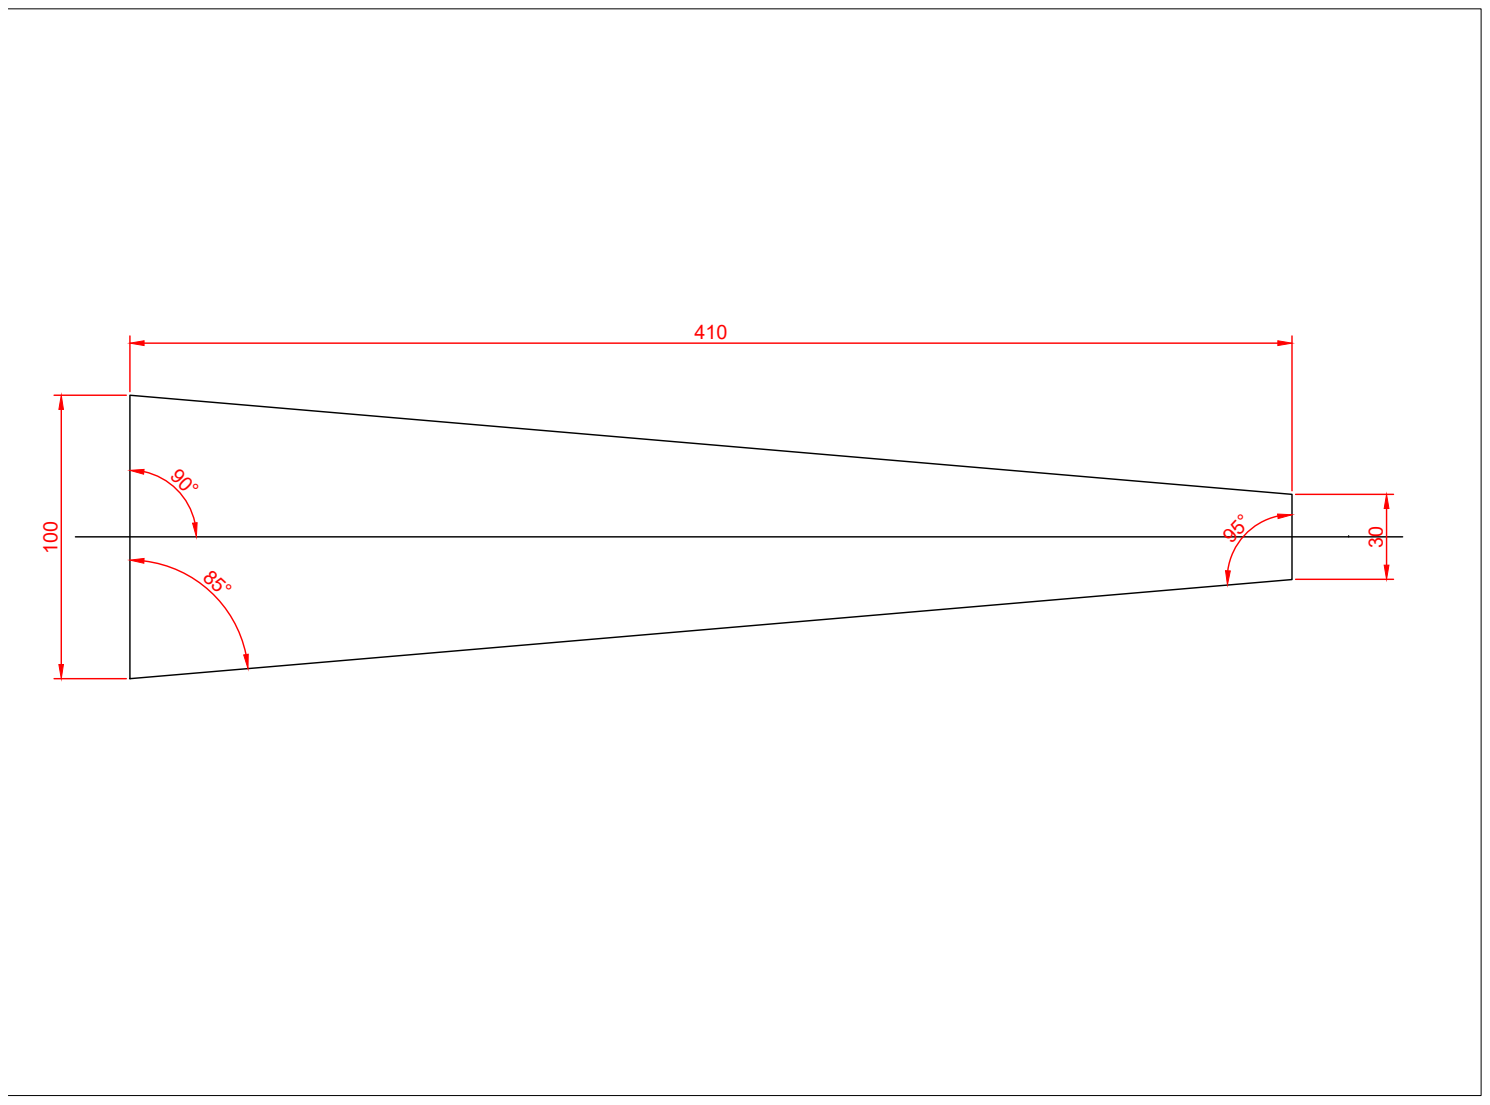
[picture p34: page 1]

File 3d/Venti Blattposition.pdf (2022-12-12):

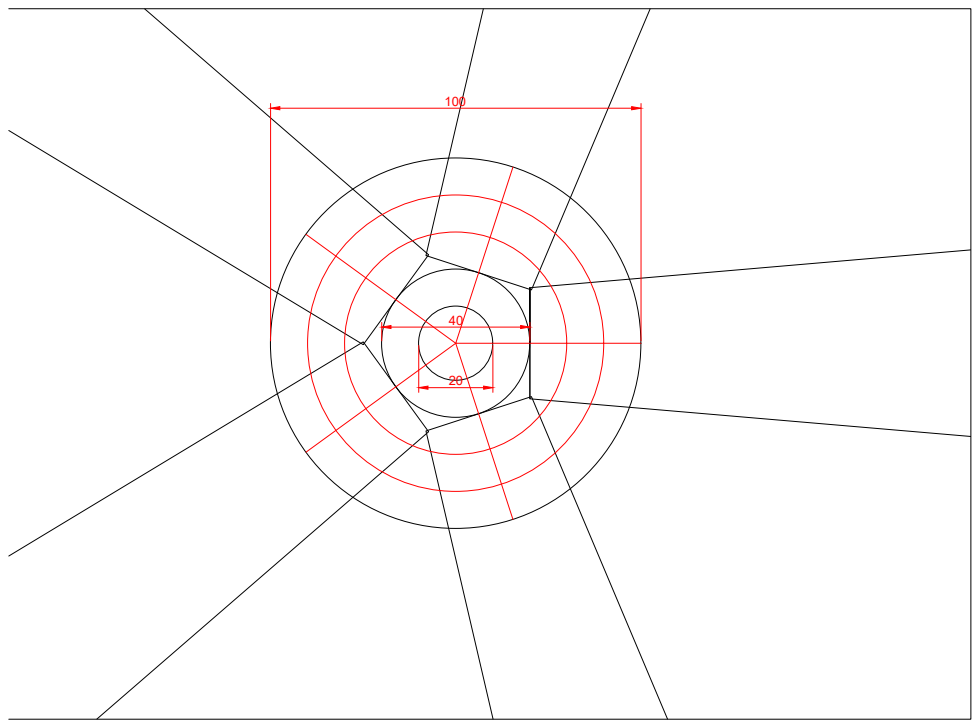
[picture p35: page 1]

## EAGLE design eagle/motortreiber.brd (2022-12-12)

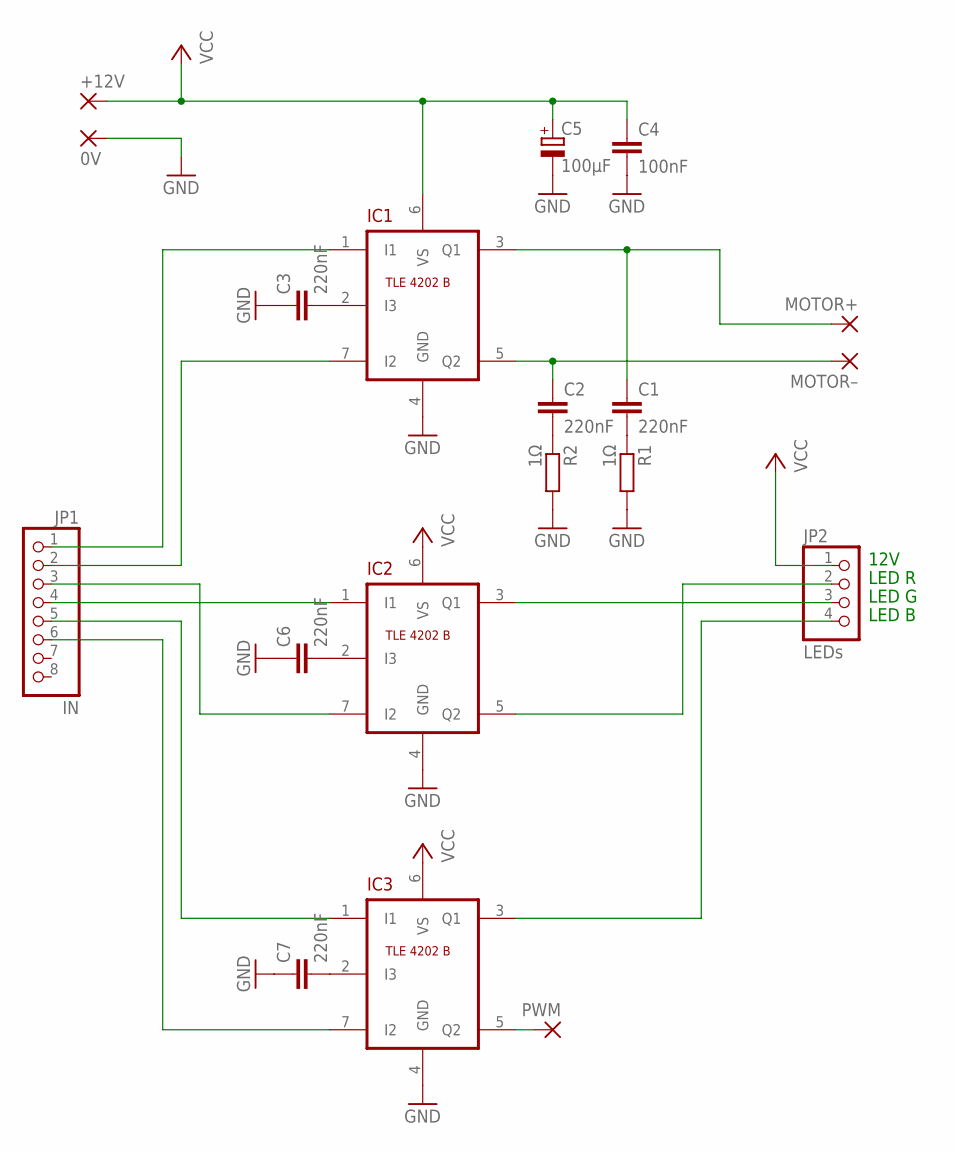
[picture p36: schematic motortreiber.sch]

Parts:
0V: WIREPAD2,15/1,0; 2,15/1,0
+12V: WIREPAD2,15/1,0; 2,15/1,0
C1, C2, C3, C6, C7: 220nF; C5B2.5
C4: 100nF; C2.5-3
C5: 100µF; E2,5-5
IC1, IC2, IC3: TLE-4202-B-100MIL; TO-220-7-BREADBOARD
JP1: IN; 1X08
JP2: LEDs; 1X04
MOTOR+: WIREPAD2,15/1,0; 2,15/1,0
MOTOR–: WIREPAD2,15/1,0; 2,15/1,0
PWM: WIREPAD2,15/1,0; 2,15/1,0
R1, R2: 1Ω; 0204/7

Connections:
GND: 0V.1, C3.1, C4.2, C5.-, C6.1, C7.1, IC1.4 (GND), IC2.4 (GND), IC3.4 (GND), R1.2, R2.2
unnamed: C1.1, IC1.3 (Q1), MOTOR+.1
unnamed: C2.1, IC1.5 (Q2), MOTOR–.1
unnamed: C3.2, IC1.2 (I3)
unnamed: IC1.1 (I1), JP1.1
unnamed: IC1.7 (I2), JP1.2
unnamed: C1.2, R1.1
unnamed: C2.2, R2.1
unnamed: IC2.1 (I1), JP1.4
unnamed: IC3.7 (I2), JP1.6
unnamed: IC3.1 (I1), JP1.5
unnamed: IC2.7 (I2), JP1.3
unnamed: C6.2, IC2.2 (I3)
unnamed: C7.2, IC3.2 (I3)
unnamed: IC3.5 (Q2), PWM.1
N$BOUT: IC3.3 (Q1), JP2.4
N$GOUT: IC2.3 (Q1), JP2.3
N$ROUT: IC2.5 (Q2), JP2.2
VCC: +12V.1, C4.1, C5.+, IC1.6 (VS), IC2.6 (VS), IC3.6 (VS), JP2.1

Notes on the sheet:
12V
LED R
LED G
LED B

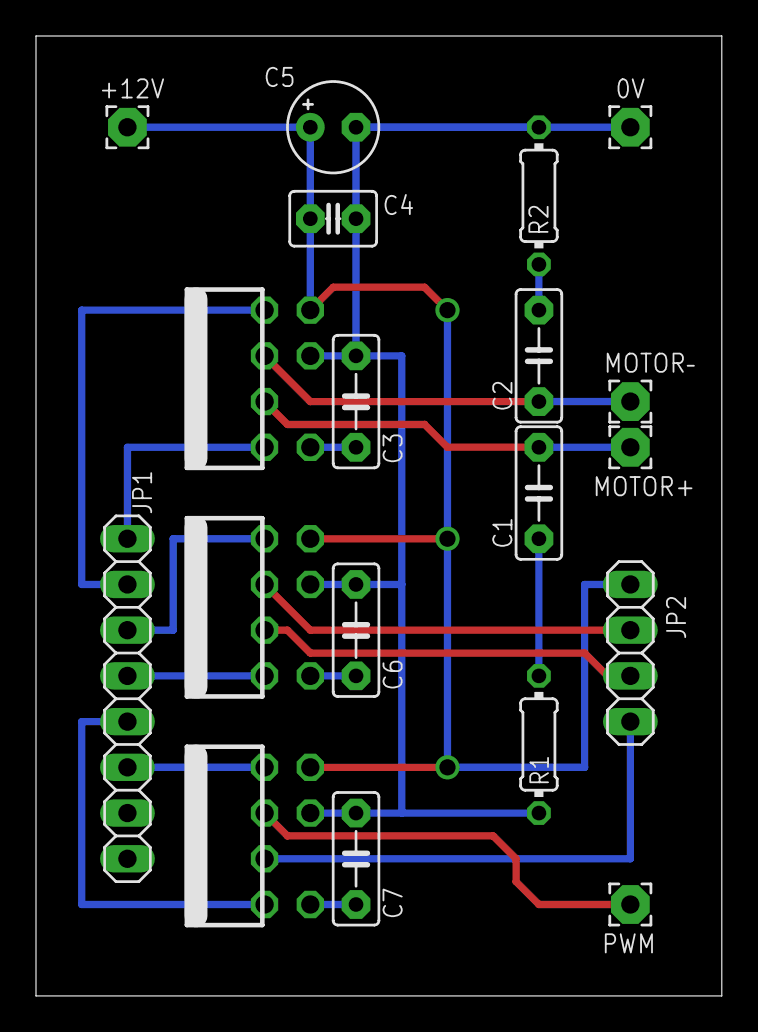
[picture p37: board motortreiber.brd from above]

Board: 2 copper layers, 38.1 x 53.3 mm, 19 parts (0 on the bottom side), 19 nets.

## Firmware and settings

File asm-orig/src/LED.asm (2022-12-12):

/**** A P P L I C A T I O N   N O T E   ************************************
*
* Title			: 9ch DMX LED PWM-Dimmer
* Last updated          : 19.09.2006
* Target		: Transceiver Rev.3.01 [ATmega8515]
*
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
 If you have no copy of the GNU General Public License, write to the 
 Free Software Foundation, Inc., 675 Mass Ave, Cambridge, MA 02139, USA. 

 For other license models, please contact the author.

;***************************************************************************/

.include "m8515def.inc"

;Register and Pin definitions

.def tempL 				= r16
.def tempH				= r17
.def Flags				= r18
.def DMXstate			= r19
.def null				= r2
.def status				= r21
.def ind_count			= r3
.def blink				= r4
.def PwmCnt				= r20
.def SREGbuf			= r5
.def ChaseFine			= r6
.def ChaseRes			= r7

.equ StrobeFreqH		= 0x80
.equ StrobeFreqL		= 0x81
.equ StrobeBuf			= 0x82

.equ OldStepH			= 0x83
.equ OldStepL			= 0x84
.equ NewStepH			= 0x85
.equ NewStepL			= 0x86
.equ StepCnt			= 0x87
.equ ChaseCnt			= 0x88
.equ ChaseSeed			= 0x89

.equ LED1= PD7
.equ LED2= PE0
.equ BIT9= PE2

.equ DMX_FIELD=      0x60 		;SRAM-Beginn
.equ DMX_CHANNELS=   10
.equ PWM_FIELD=      0x70		
.equ F_OSC=          8000
.equ FLASH_DURATION= 400
.equ IND_OFFSET=     12	 	;Offset für indicator-Timer (14Hz)

#define CHS_SPD		 (0x600)
#define RATE         (0x500)
#define PAT0		 (0x400)
#define PAT1         (PAT0 +0xA)
#define PAT2		 (PAT1 +0xA)
#define PAT3		 (PAT2 +0xA)
#define PAT4		 (PAT3 +0xA)
#define PAT5         (PAT4 +0xA)
#define PAT6         (PAT5 +0xA)
#define PAT7         (PAT6 +0xA)


;***** special Flags

#define  VALID_DMX 	    (0)
#define  SIGNAL_COMING  (1)

#define  doIND			(5)
#define  BLACK_OUT		(6)
#define  DATA_REFRESHED (7)


;interrupt vectors
.org 0	
	rjmp init 		;reset vector address
	reti			;External Interrupt0 Vector Address
	reti			;External Interrupt1 Vector Address
	reti			;Input Capture1 Interrupt Vector Address
	rjmp strobe		;Output Compare1A Interrupt Vector Address
	reti			;Output Compare1B Interrupt Vector Address
	reti			;Overflow1 Interrupt Vector Address
	rjmp pwm		;Overflow0 Interrupt Vector Address
	reti			;SPI Interrupt Vector Address
	rjmp get_byte	;UART Receive Complete Interrupt Vector Address
	reti			;UART Data Register Empty Interrupt Vector Address
	reti			;UART Transmit Complete Interrupt Vector Address
	reti			;Analog Comparator Interrupt Vector Address
	reti			;External Interrupt2 Vector Address
	reti			;Output Compare0 Interrupt Vector Address
	reti			; EEPROM Interrupt Vector Address
	reti			; SPM complete Interrupt Vector Address
	reti			; SPM complete Interrupt Vector Address

; INIT

init:

; Stack
	ldi		tempH,high(RAMEND)
	ldi		tempL,low(RAMEND)
	out		SPH,tempH
	out		SPL,tempL

; WATCHDOG
	wdr
	ldi 	tempL, (1<<WDE)|(1<<WDCE)
	out 	WDTCR, tempL
	ldi 	tempL, (1<<WDE)|(1<<WDCE)|(1<<WDP2)|(1<<WDP1)
	out 	WDTCR, tempL
	wdr												;set prescaler @0,5s

; PortA
	ser 	tempL
	out 	DDRA, tempL
	clr 	tempL
	out 	PortA, tempL 							;low Outputs

; PortB
	ldi		tempL, 0b00000011
	out		DDRB, tempL
	ldi		tempL, 0b11110100
	out		PortB, tempL

; PortD
	ldi 	tempL, 0b10000100
	out 	DDRD, tempL
	ldi 	tempL, 0b01111000
	out 	PortD, tempL 							;DMX & Spare , LED1 on

; PortE
	ldi 	tempL, 0b00000001
	out 	DDRE, tempL
	ser		tempL
	out 	PortE, tempL 							;LED2 off, BIT9 & OPTION Pullup

; Timers
	ldi 	tempL, (1<<CS01)						;set counter0 @clock/8 frequency
	out 	TCCR0, tempL
	clr		tempL
	out		TCCR1A, tempL
	ldi 	tempL, (1<<CS12)|(1<<WGM12) 			;set counter1 @clock/256 frequency, CTCmode
	out 	TCCR1B, tempL
	ldi 	tempL, 	(1<<TOIE0)						;aktivate overflow interrupt
	out 	TIMSK, tempL
		
	rcall	init_dmx
	
	
; set Register
	clr null
	clr blink
	com blink
	mov	ChaseFine, blink
	ldi tempL, IND_OFFSET
	mov ind_count, tempL
	ldi PwmCnt, 0xFF
	ldi	Flags, 0									;clear Flags
	
	sts StepCnt, null
	sts	NewStepH, null
	sts NewStepL, null
	ldi	tempL, 1
	sts ChaseCnt, tempL
	sts ChaseSeed, tempL
	mov	ChaseRes, tempL		

	wdr
	sei

main: 	sbrc	Flags, doIND
		rcall	indicate

		rcall   eval_strobe_freq
;rcall chase
		rjmp	main



;****************************** LED INDICATOR ***********************************
indicate:
		cbr		Flags, (1<<doIND)	;clear flag
		rcall	chase
		dec		ind_count
		breq	ind_a
		ret
      
	  ind_a:
		wdr							;reset Watchdog
;working LED
		sbrc	Flags, DATA_REFRESHED	;should flash?
		rjmp	data_flash	
		sbi		PortE, LED2			; LED off

Error_LED:
		sbrc  	blink, 0			;wenn erstes bit HI
		rjmp  	on
		sbi   	PortD, LED1
		rjmp  	ind_tst
	 on:
	 	cbi  	PortD, LED1

     ind_tst:
	    lsr   	blink
		ldi		tempL, 1
		cp		blink, tempL
		brne	no_ind
	 		 	
;wenn durchrotiert (blink = 0)
		ldi		tempL, 0b10000000		
		sbrs 	Flags, VALID_DMX
		ldi	 	tempL, 0b10001010
		sbrs 	Flags, SIGNAL_COMING
		ldi	 	tempL, 0b10000010
		mov  	blink, tempL

		cbr 	Flags, (1<<VALID_DMX)|(1<<SIGNAL_COMING)
	
	no_ind:
		ldi		tempL, IND_OFFSET
		mov		ind_count, tempL		;plant prescaler
		ret
	data_flash:
		cbr		Flags, (1<<DATA_REFRESHED)
	    sbis 	PortE,LED2				;blinken grün
		rjmp 	off
		cbi		PortE,LED2
		rjmp 	Error_LED
		off:
		sbi 	PortE,LED2
		rjmp 	Error_LED 




;****************************** strobe frequency ***********************************
eval_strobe_freq:
		lds		tempL, DMX_FIELD					;get 1st DMX ch
		cpi		tempL, 246
		brlo	esf_1
		ldi		tempL, 245
       esf_1:
		lds		tempH, StrobeBuf
		cp		tempL, tempH
		brne	esf_2								;only eval if changed
		ret
	esf_2:
		sts		StrobeBuf, tempL
		cpi		tempL, 30
		brlo	esf_no_strobe
		cpi		tempL, 245
		brsh	esf_sync

		subi	tempL, 30							;0-200 allowed
		ldi		ZL, low(RATE*2)						;get freq from table
		ldi		ZH, high(RATE*2)
		add		ZL, tempL
		adc		ZH, null
		add		ZL, tempL
		adc		ZH, null
		lpm		tempL, Z+
		lpm		tempH, Z
		cli
		sts		StrobeFreqL, tempL					;atomic store
		sts		StrobeFreqH, tempH
		
		in		tempL, TIMSK
		sbr		tempL, (1<<OCIE1A)					;enable irq
		out		TIMSK, tempL
		in		tempL, TIFR
		sbr		tempL, (1<<OCF1A)					;enable irq
		out		TIFR, tempL
		reti	


	esf_no_strobe:
		in		tempL, TIMSK
		cbr		tempL, (1<<OCIE1A)					;disable irq
		out		TIMSK, tempL
		cbr		Flags, (1<<BLACK_OUT)				;enable pwm
		ret
	
	esf_sync:
		in		tempL, TIMSK
		sbrs	tempL, OCIE1A						;only when strobing
		ret
		cli
		sbr		Flags, (1<<BLACK_OUT)				;blank!
		lds		ZH, StrobeFreqH
		lds		ZL, StrobeFreqL
		out		OCR1AH, ZH
		out		OCR1AL, ZL
		sbiw	ZH:ZL, 20
		out		TCNT1H, ZH
		out		TCNT1L, ZL 		
		reti
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

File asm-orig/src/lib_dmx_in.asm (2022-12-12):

;**** A P P L I C A T I O N   N O T E   ************************************
;*
;* Title		: DMX512 reception library
;* Version		: v1.2
;* Last updated	        : 04.06.06
;* Target		: Transceiver Rev.3.01 [ATmega8515]
;*
;* written by hendrik hoelscher, www.hoelscher-hi.de
;***************************************************************************
; This program is free software; you can redistribute it and/or 
; modify it under the terms of the GNU General Public License 
; as published by the Free Software Foundation; either version2 of 
; the License, or (at your option) any later version. 
;
; This program is distributed in the hope that it will be useful, 
; but WITHOUT ANY WARRANTY; without even the implied warranty of 
; MERCHANTABILITY or FITNESS FOR A PARTICULAR PURPOSE. See the GNU 
; General Public License for more details. 
;
; If you have no copy of the GNU General Public License, write to the 
; Free Software Foundation, Inc., 675 Mass Ave, Cambridge, MA 02139, USA. 
;
; For other license models, please contact the author.
;
;***************************************************************************

 /************* Definitions in main source **********************
		
		#define DMX_FIELD	 0x60	//base address of DMX array
		#define DMX_CHANNELS 8		//no. of channels
		#define DMX_CHANGED  0		//DMX flag: indicates ch changes
		#define DMX_BT_CH	 1		//internal flag
		#define DMXstate	 R18	//status reg for DMX-ISR (r16-r31)
	  //X-Pointer reserved for DMX ISR!!

		#define F_OSC		 8000  	//oscillator freq. in kHz (typical 8MHz or 16MHz)

 **************************************************************/

	
init_dmx:
	;**** PortD
		in		tempL, DDRD
		sbr		tempL, (1<<2)
		out		DDRD, tempL
		in		tempL, PortD
		cbr		tempL, (1<<2)		;enable reception
		out		PortD, tempL		
	;**** USART
    	ldi 	tempL, ((F_OSC/4000)-1) ;set Usart to 250 kbaud
    	out 	UBRRL, tempL
    	clr 	tempL
    	out 	UBRRH, tempL
    	ldi 	tempL, (1<<URSEL)|(3<<UCSZ0)|(1<<USBS)
    	out 	UCSRC, tempL			
		in		tempL,UDR
 		clr		tempL
		out		UCSRA,tempL		
		sbi 	UCSRB,RXCIE
		sbi 	UCSRB,RXEN			

#ifndef USE_ADR
	;**** PortC
		clr 	tempL
		out 	DDRC, tempL
		ser 	tempL
		out 	PortC, tempL  		;Inputs with PullUp for DipSwitch
	;**** PortE
		in		tempL, DDRE
		cbr	 	tempL, (1<<1)|(1<<2)
		out 	DDRE, tempL
		in		tempL, PortE
		sbr	 	tempL, (1<<1)|(1<<2)
		out 	PortE, tempL 		;PE2 & OPTION Pullup
#endif

	;**** memory
		ldi		XH, high(DMX_FIELD)
		ldi		XL,  low(DMX_FIELD)
		ldi		tempL,0x00			;set all channels to 0
		ldi 	DMXstate, DMX_CHANNELS
	write_RxD:	
		st 		X+,tempL
		dec		DMXstate
		brne	write_RxD

	//	clr 	DMXstate			;set DMXstate to 'wait for Reset' (done by counting ;-)
		ret


/* ***********************************************************************************************************
 *					DMX reception ISR
 ************************************************************************************************************/
get_byte:
		in      SREGbuf, SREG
		push	tempH
		push	tempL		

		in		tempL,UCSRA		;get status register before data register
		in		tempH,UDR
#ifdef SIGNAL_COMING
		sbr		Flags, (1<<SIGNAL_COMING)	;indicator flag: USART triggered
#endif	
		sbrc	tempL,DOR		;check for overrun -> wait for reset
		rjmp	overrun	

		sbrc	tempL,FE		;check for frame error -> got reset
		rjmp	frame_error	
		
		cpi		DMXstate, 1   	;check for startbyte (must be 0)
		breq	startbyte

  		cpi 	DMXstate, 2   	;check for start adress
		breq    startadr
  		
 		cpi 	DMXstate, 3	
  		brsh	handle_byte

	gb_finish:
		pop		tempL
		pop		tempH
		out     SREG, SREGbuf	
		reti			

	startbyte:
		tst 	tempH	 				;if null-> Startbyte
		brne 	overrun
		inc  	DMXstate 				;next -> start address

#ifndef USE_ADR
		in 		XL, PinC 				;get start address
		com     XL
		clr		XH
		sbis	PinE, PE2				;9th bit
		inc		XH
#endif
#ifdef USE_ADR
		rcall	get_address
#endif
		rjmp	gb_finish

 	startadr:
		sbiw	XH:XL, 1
		brne	gb_finish
		ldi 	XH, high(DMX_FIELD)
		ldi		XL,  low(DMX_FIELD)
		inc  	DMXstate 				;next-> data handler
		
	handle_byte:
#ifdef DMX_EXT							;external manipulation of DMX data?
		rcall	clc_dmx
#endif			
		ld		tempL, X				;get old val
		cp		tempL, tempH
		breq	gb_noChange
		st		X, tempH
#ifdef DATA_REFRESHED
		sbr		Flags, (1<<DATA_REFRESHED) ;indicator flag: ch changed
#endif
       gb_noChange:
	    adiw	XH:XL, 1

		cpi		XL, low(DMX_FIELD +DMX_CHANNELS)
		brne	gb_finish
		cpi		XH, high(DMX_FIELD +DMX_CHANNELS)
		brne	gb_finish
#ifdef VALID_DMX
		sbr		Flags, (1<<VALID_DMX)	;indicator flag: all ch received
#endif	
		clr		DMXstate
		rjmp	gb_finish
	
 	frame_error:
		ldi 	DMXstate, 1				;FE detected as break
		cbi		UCSRA,FE				;further framing errors, caused by longer breaks
		rjmp	gb_finish

	overrun:
	 	clr 	DMXstate				;wait for frame-error
		cbi		UCSRA,DOR				
		rjmp	gb_finish
